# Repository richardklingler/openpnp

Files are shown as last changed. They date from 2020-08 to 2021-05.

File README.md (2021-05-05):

## My OpenPnP pick and place machine stuff

This is a place where a publish all my work building a pick and place machine including mechanics, electronics, Marlin firmware modifications and 3D printed designs.

The machine is driven by the excellent and open sourced [OpenPNP software](http://openpnp.org).

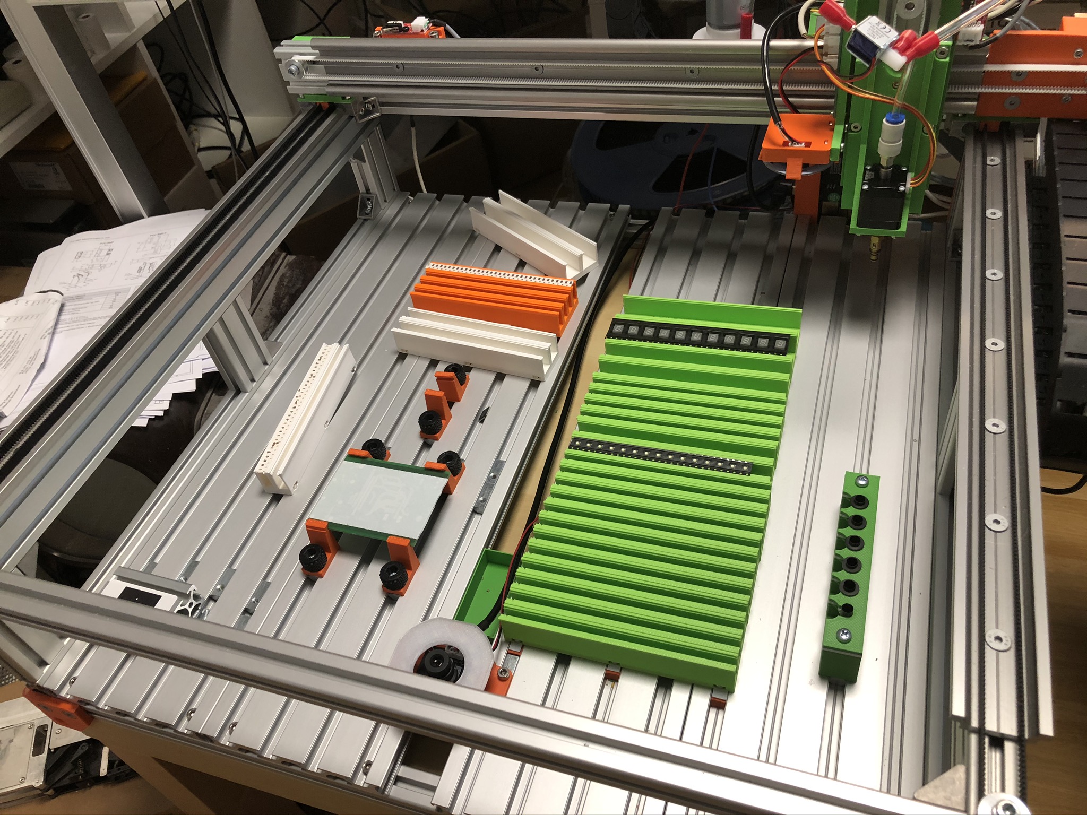
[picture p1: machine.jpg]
My pick and place machine running OpenPNP


### Sponsoring

All required hardware is financed with my low little budget, so every donation is very welcome, either through the Patreon link on the side or through Paypal Me:

[Paypal Me](https://paypal.me/renderingfun)

Currently work is on hold due to missing funds.

### Things to do

This is still a work-in-progress project, so not everything is either published or at final stage. Currently following tasks are ongoing:

#### Z-axis rework

Currently the Z-axis uses Igus slider which are showing high tolerances when pushed/pulled in Y direction. The rails will be therefore replaced with dual MGN9 rails with 2 carriages each for better stability/accuracy. A dual rail design could then also be used for a dual-nozzle setup.

#### X-axis rework

Also the Igus rails on the X-axis are unacceptable. Seems Igus rails are only halfway usable when lying flat, just like for the Y-axis. The new X-axis will use two MGN9 rails, one on top and one at the bottom of the X-axis profile.

### Updates

- 12.09.2020 : Added X belt tensioner mount
- 24.08.2020 : Added vacuum pump mount
- 23.08.2020 : Added OpenSCAD designs for electronics
- 23.08.2020 : Added Y axis OpenSCAD design files
- 15.08.2020 : Updated Tool Changer design
- 14.08.2020 : Added OpenSCAD Camera Mounts
- 14.08.2020 : Added OpenSCAD CP40 Nozzle Holder

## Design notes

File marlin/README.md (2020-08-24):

## Marlin modifications for using with OpenPNP

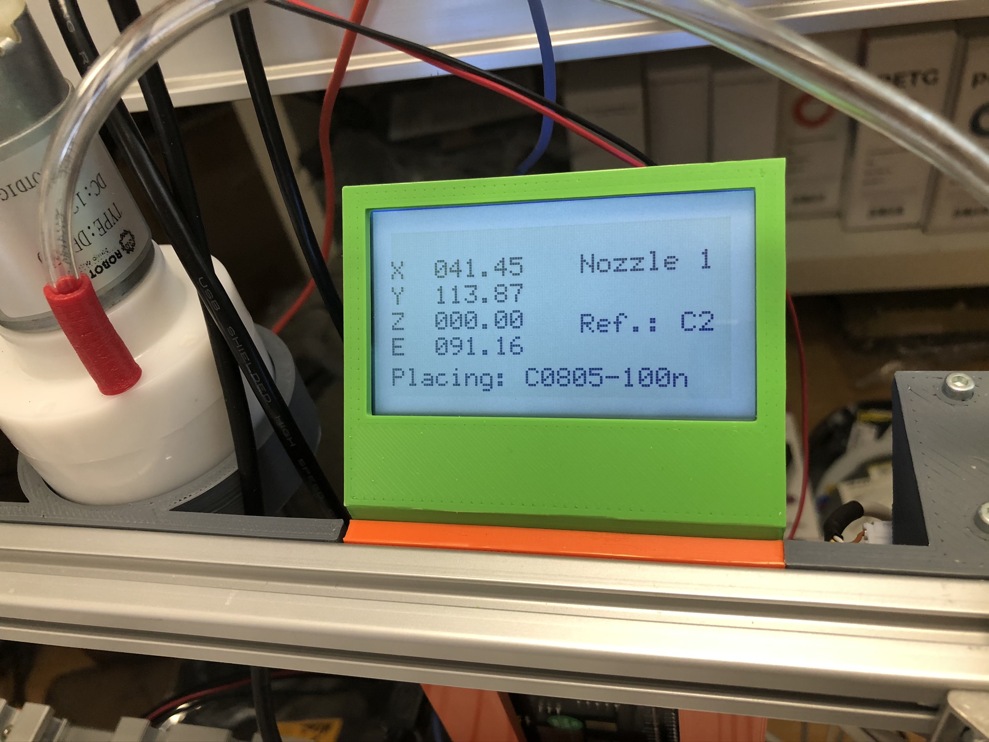
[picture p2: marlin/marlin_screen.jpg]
Marlin Status Screen


Normally Marlin firmware is meant for running a 3d printer, though it has some configuration options to be used for CNC milling and laser cutters.

The most obvious changes are:

- Add dual stepper for Y-axis
- Home position of Z-axis at Z-Max. The Z-axis moves down starting at 0.
- Change XYZ homing bump speed
- Configure outputs to be used for vacuum pump, vacuum valve and LED lighting

The not so easy modifications are for the LCD status screen where we just want to display all coordinates together with what the machine is doing. All 3d printer related icons are removed.

- Remove 3d printer icons
- Layout all coordinates vertically with XXX.XX precision
- Modify the M117 status message Gcode command to add more messages on the screen

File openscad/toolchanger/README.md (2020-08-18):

## Tool Changer for CP40 nozzles

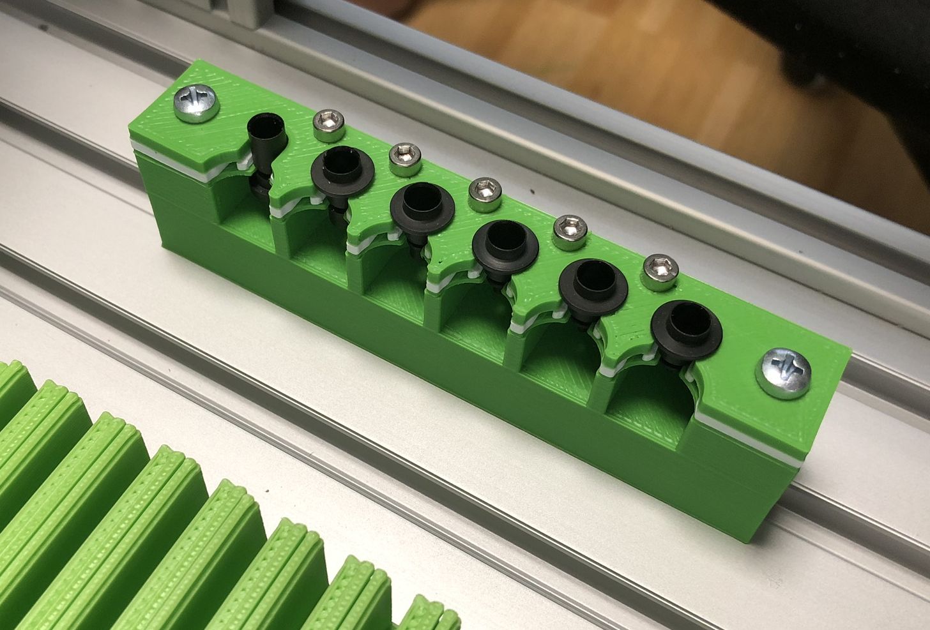
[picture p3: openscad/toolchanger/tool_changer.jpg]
CP40 tool Changer


This is a simple design for CP40 nozzle holder.
The number and the distance betwwen nozzles is configurable in OpenSCAD.

This design uses 4 parts for this:

- Tool_Changer_Mount.scad: Bottom part for mounting all 4 parts to the table. Height has to be adjusted to your needs.
- Tool_Changer_Bottom,scad: A thin layer of 1mm where the nozzles slide in, the thickness is adjusted with the 's' parameter
- Tool_Changer_Middle.scad: This part uses a clamp mechanism so that nozzles stay in place. The force of the clamp can be adjusted with the 'o' parameter'
- Tool_Changer_Top.scad: Top layer which will be screwed down to the table with all other parts

Here is a YouTube video showing how it works:

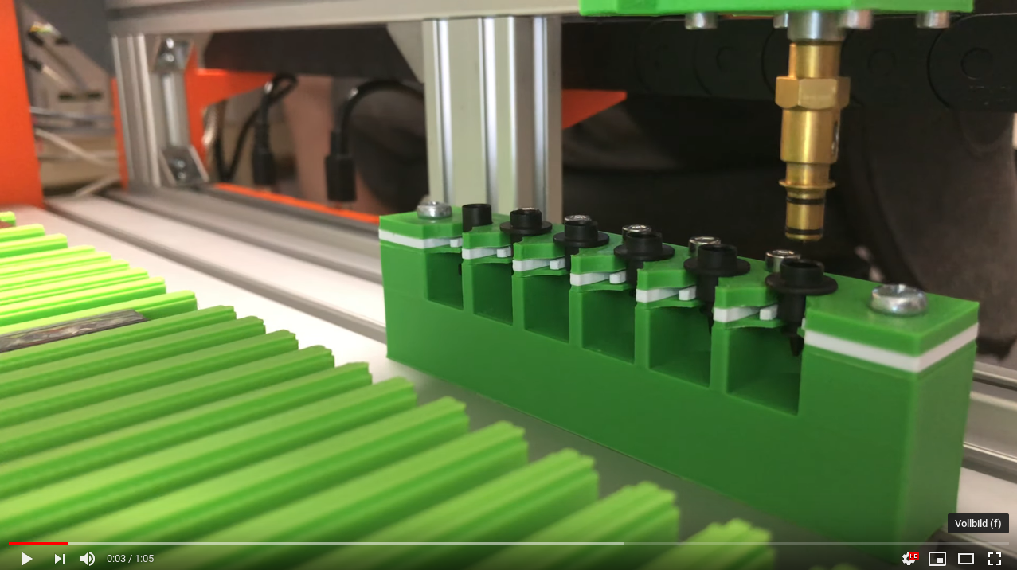
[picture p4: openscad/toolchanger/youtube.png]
CP40 tool changer in action (https://youtu.be/qcL0MLGex4M "CP40 Nozzle Changer")


### 3D Printing

I have printed all parts excep the middler layer which clamps the nozzles with ASA material for its strength.
The clamp itself was printed in PETG as with ASA it starts to bend during printing when you don't use or have a chamber like me (o;

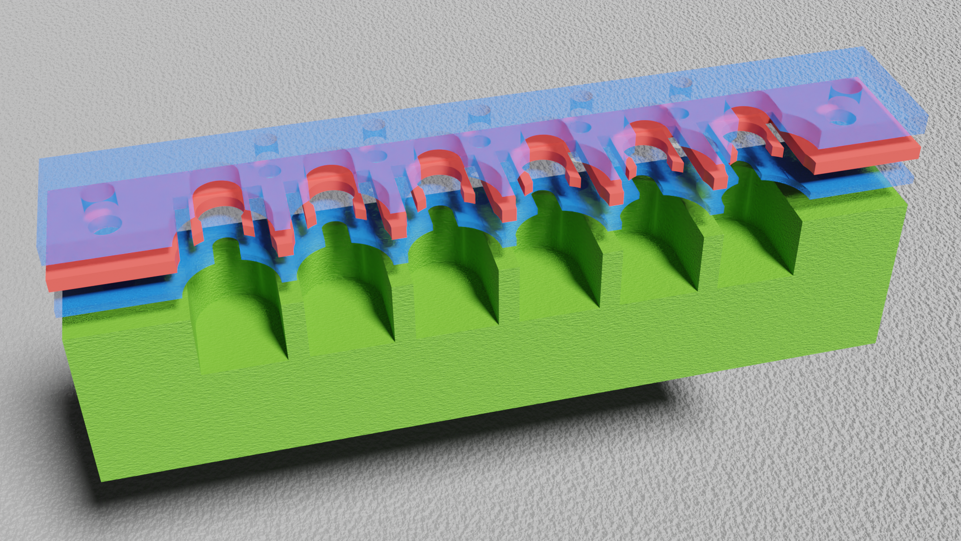
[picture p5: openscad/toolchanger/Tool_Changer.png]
CP40 tool Changer


### Assembly

To mount the tool changer on the machine's table I used M4 x 45 screws....
For clamping all layers together you would (Number of nozzles - 1) M3 x 16 screws and a M3 nut which slides in the bottom mount block at the back.

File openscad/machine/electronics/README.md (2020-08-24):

## Electronics

Here are the OpenSCAD design files for attaching various electronic components to the machine.

### PCB mount for BTT SKR v1.4

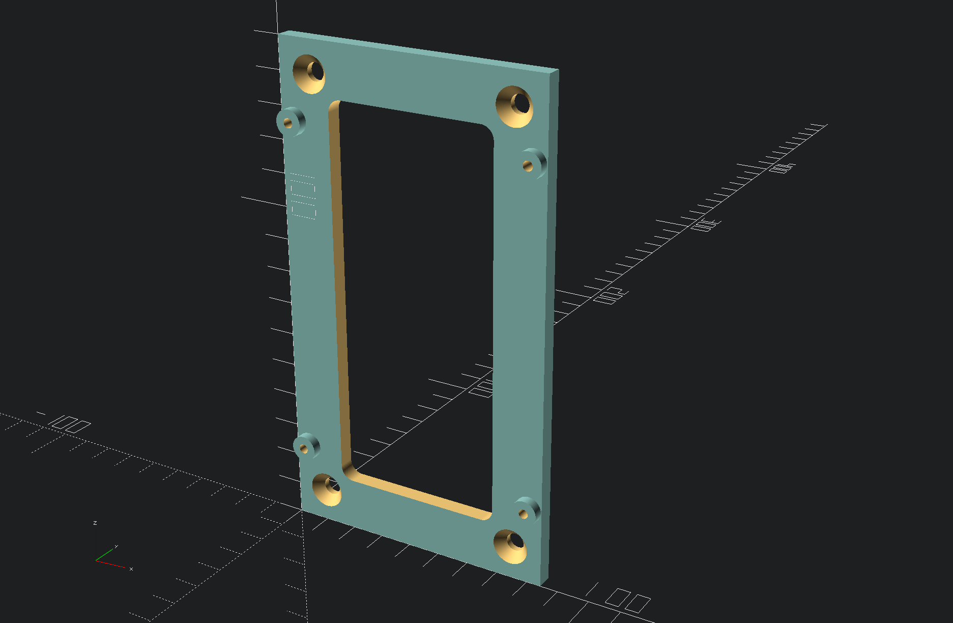
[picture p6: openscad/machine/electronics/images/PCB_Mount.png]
BTT SKR v1.4 mount


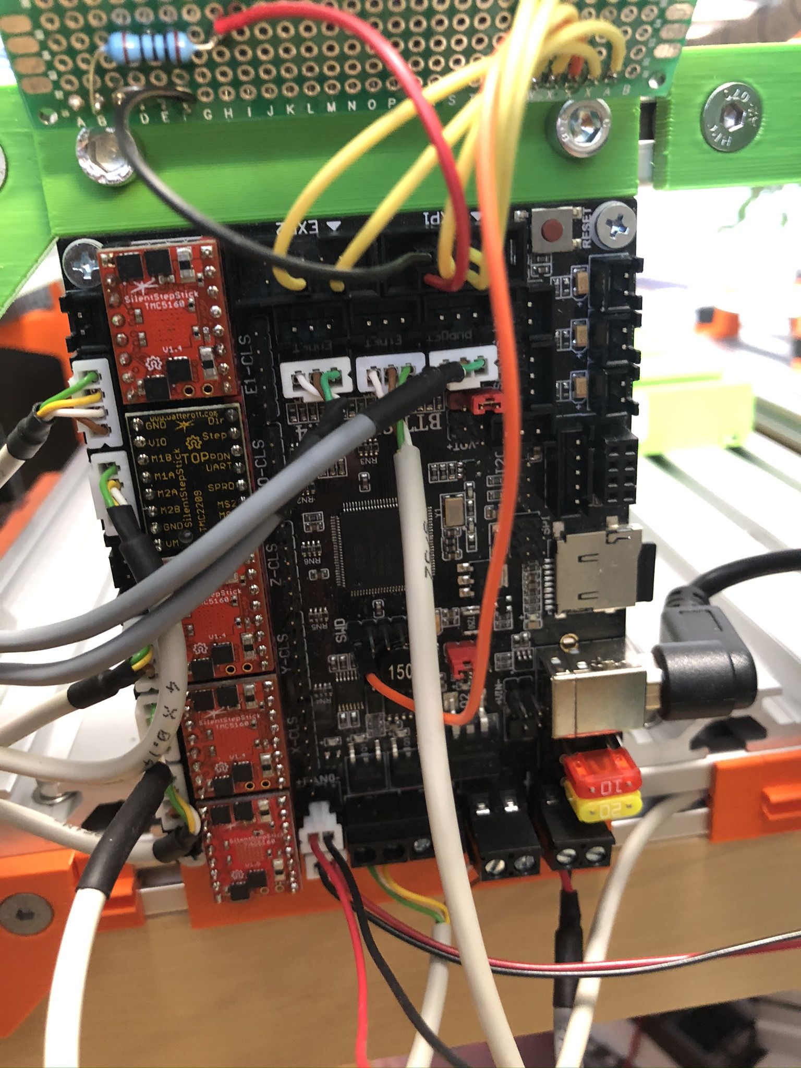
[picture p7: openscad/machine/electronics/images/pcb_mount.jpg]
BTT SKR v1.4 mount


### LCD mount for Newhaven 12864 LC display

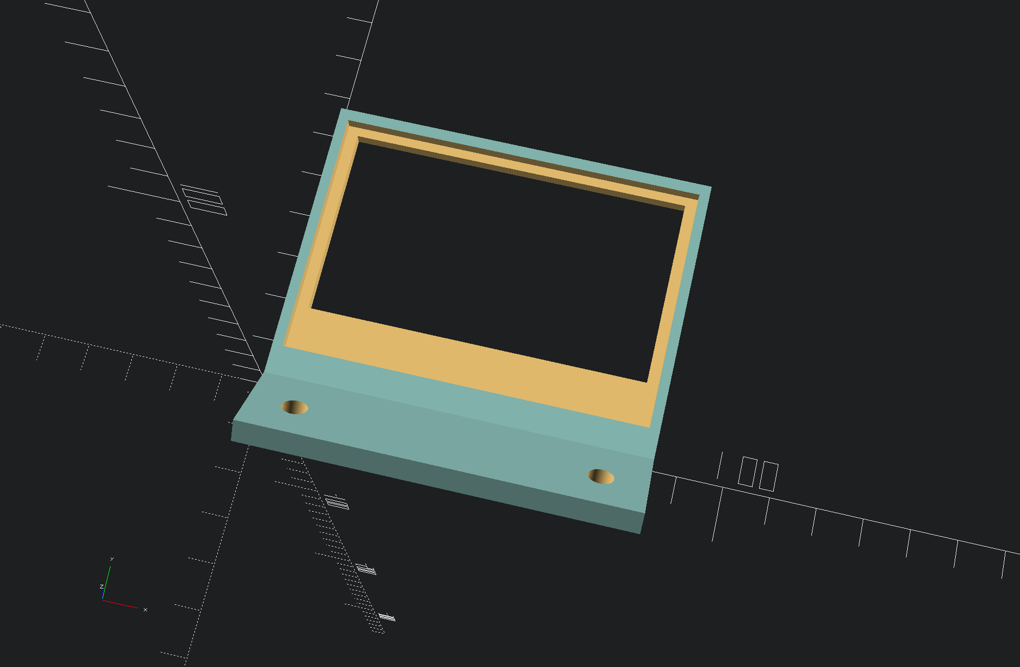
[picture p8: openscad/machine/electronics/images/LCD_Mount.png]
LCD mount


This is a holder for the Newhaven LC display INHD-C12864-1Z-FSW-FB-HTT. It is meant to screw it at the top of the PCB holder as a PCB holder with LCD mount wasn't really printable, so I did a two-part design.

### Power supply mount

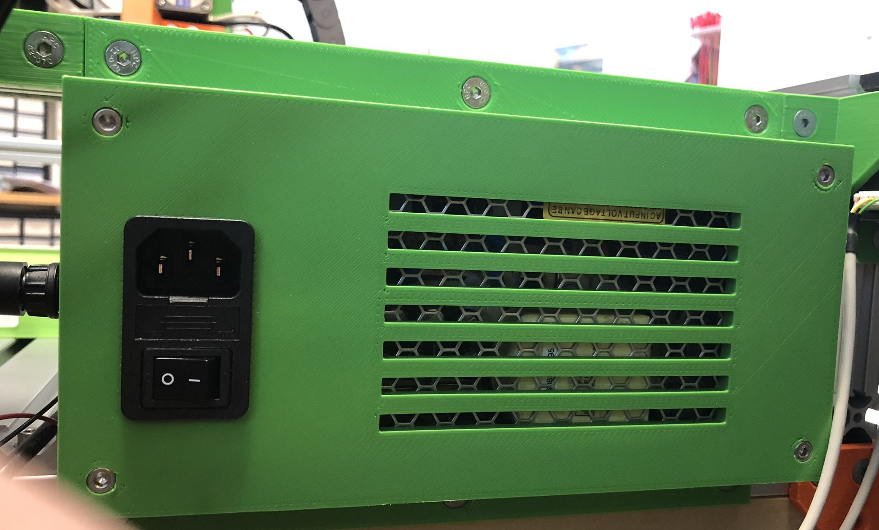
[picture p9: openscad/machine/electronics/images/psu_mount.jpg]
PSU mount


### Vacuum pump holder

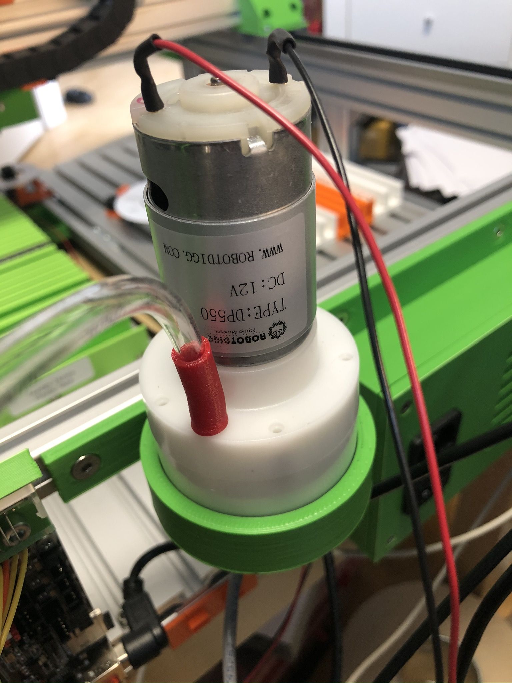
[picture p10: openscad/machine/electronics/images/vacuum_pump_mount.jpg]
Vacuum pump mount


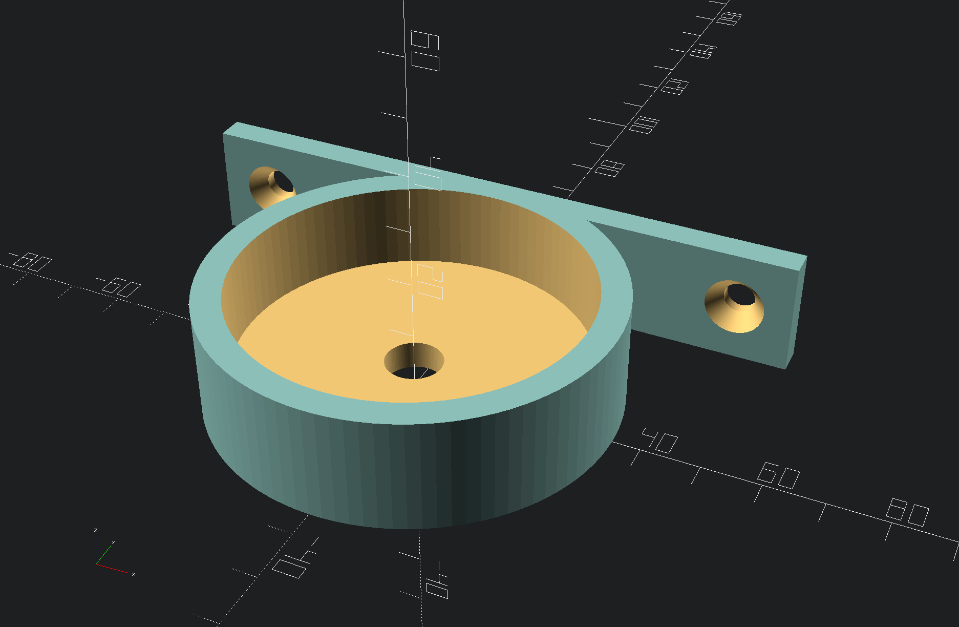
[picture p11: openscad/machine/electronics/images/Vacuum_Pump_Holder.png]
Vacuum pump mount


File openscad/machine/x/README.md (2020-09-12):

## X axis

Here you find my OpenSCAD design files in regards to the X-axis setup.

Be aware that the resulting STL files might give different results in your 3D printer due to different nozzle width and printer settings.

### X belt tensioner

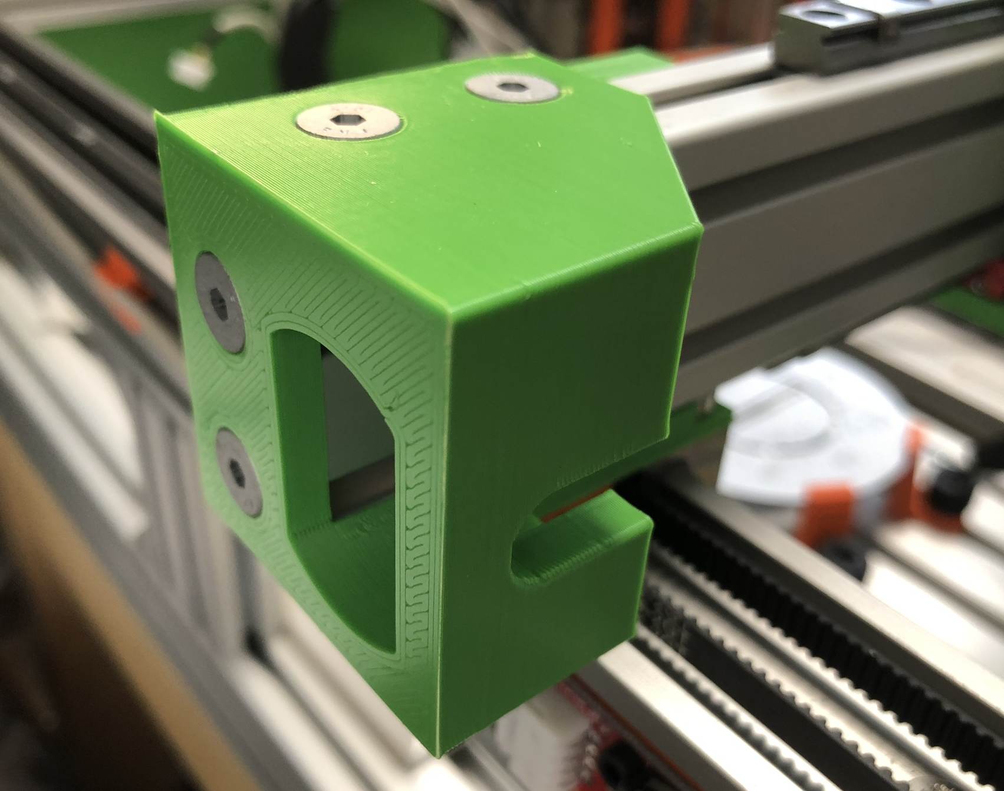
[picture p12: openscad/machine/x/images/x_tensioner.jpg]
X belt tensioner


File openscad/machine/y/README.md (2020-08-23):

## Y axis

Here you find my OpenSCAD design files in regards to the dual Y-axis setup.

Be aware that the resulting STL files might give different results in your 3D printer due to different nozzle width and printer settings.

### Y motor mount

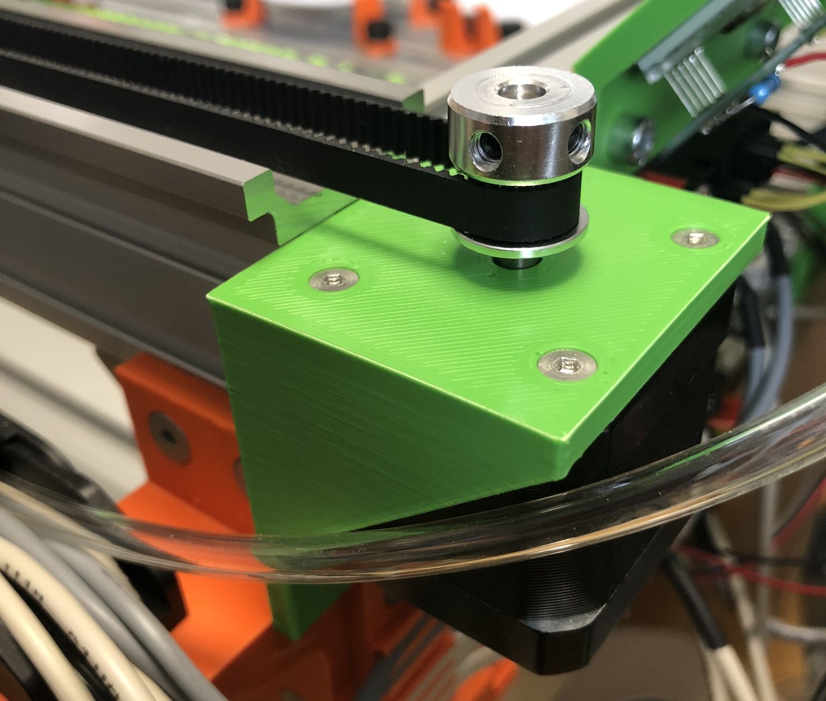
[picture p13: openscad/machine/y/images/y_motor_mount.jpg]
Y Motor Mount


The Y motor mount takes a Nema 17 motor with a width of 42mm mounted with 4 M3x8 counter sunk head screws. It is mounted with 3 M5x10 counter sunk head screws directly at the back of machine on the aluminum frame. There is only one design file, so for printing both sides you have to mirror one mesh in your slicer software.

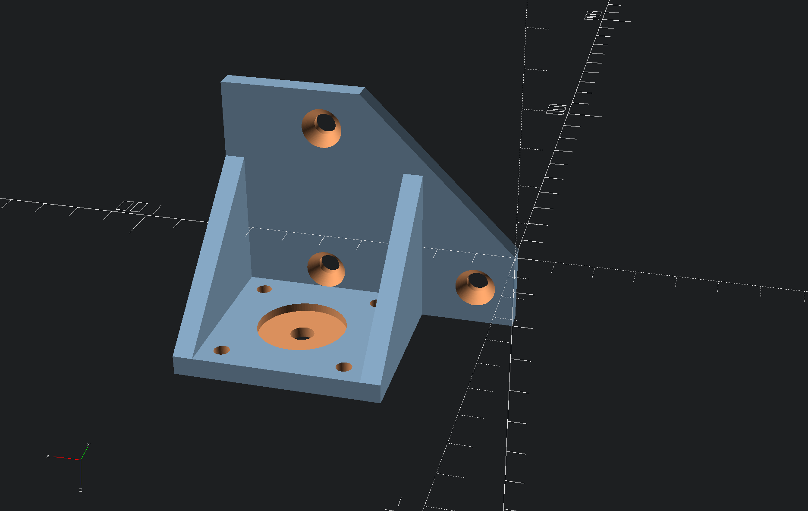
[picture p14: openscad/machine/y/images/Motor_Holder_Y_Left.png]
Y Motor Mount


### Y belt tensioner

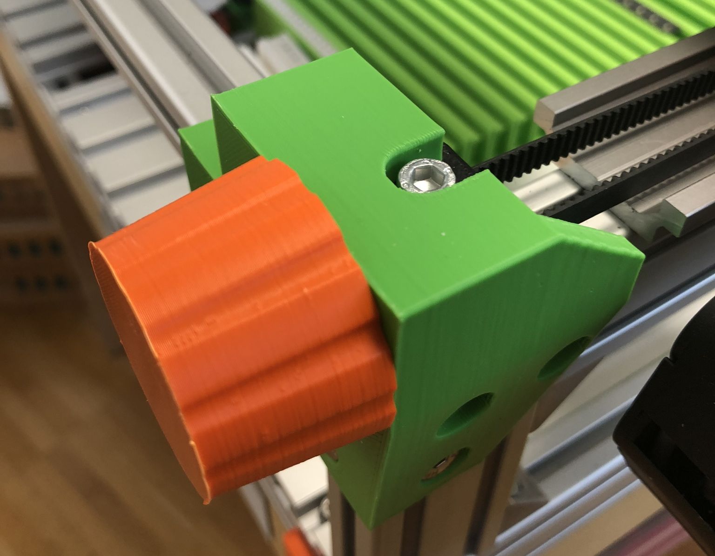
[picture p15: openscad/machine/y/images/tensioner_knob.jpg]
Y Belt Tensioner


The belt tensioner for the y-axis consists of three parts:

    - Tensioner screw
    - Tensioner knob
    - Tensioner mount

For the thread I used this thingiverse OpenSCAD library:

[OpenScad library. Threads for screws and nuts V1](https://www.thingiverse.com/thing:3131126)

For better durability I printed those parts (as most parts of my machine) with ASA filament. It is advisable to print the screw and the knob with a layer height not greater than 0.2mm. Also for both sides for the tensioner mount you have to mirror one mesh in your slicer.

### X rail mounts

The X rail mounts are designed to be screwed directly onto Igus slider blocks. Also they hold at the bottom the GT2 belt clamp mechanism. Igus rails were chosen for the Y-axis as a 6mm wide GT2 belt fits perfectly between rails and slider block.

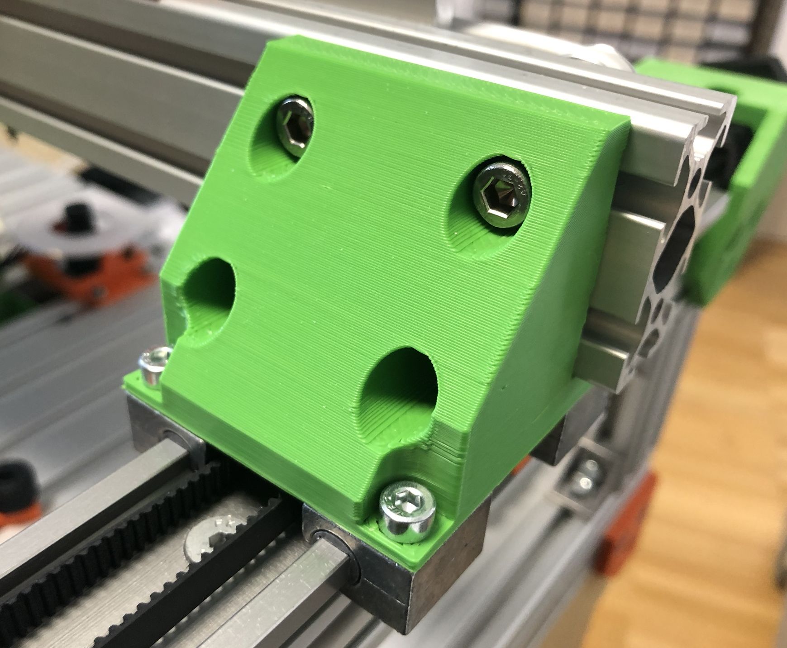
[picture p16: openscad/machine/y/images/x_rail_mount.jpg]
X Rail Mount


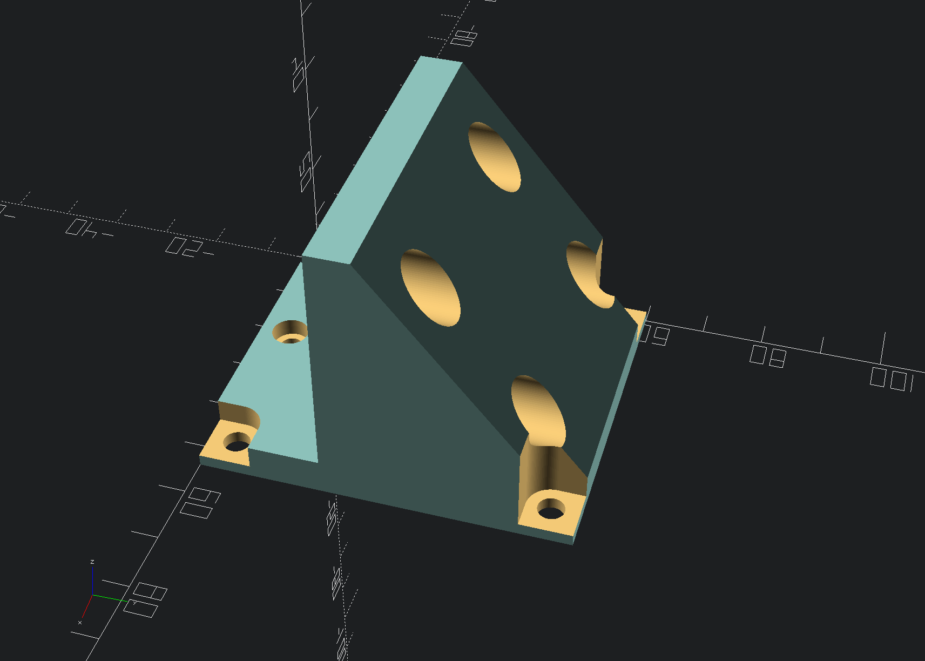
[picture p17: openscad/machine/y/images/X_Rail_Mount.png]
X Rail Mount


### GT2 clamp

This is a preliminary design as I think that it might be the cause for some backslash in the Y-axis.

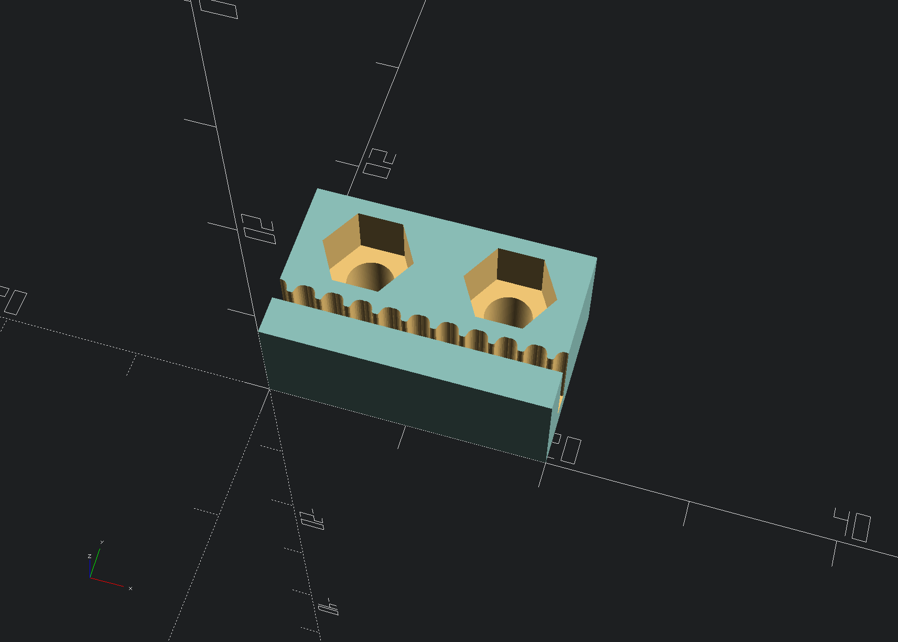
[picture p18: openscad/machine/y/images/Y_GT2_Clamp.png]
Y belt GT2 clamp


The GT2 clamp which mounts directly under the X-rail mounts uses a GT2 timing belt OpenSCAD module used for cutting out the profile. Depending on the thickness of the belt you might want to adjust this section:

    translate([-2, 3.35, 6]) belt_len(profile = tGT2_2, belt_width = 8, len = 100);
    translate([-2.2, 3.5, 6]) belt_len(profile = tGT2_2, belt_width = 8, len = 100);
    translate([-1.9, 3.5, 6]) belt_len(profile = tGT2_2, belt_width = 8, len = 100);

It just cuts out the GT2 slot at slightly different location to accommodate for thicker belts. You might want to do some test prints and check with your GT2 belt if it fits perfectly and doesn't causes any backslash.

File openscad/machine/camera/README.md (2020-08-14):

## Camera mounts

This directory contains OpenSCAD design files for my camera mounts and a LED diffuser.

### Bottom mount

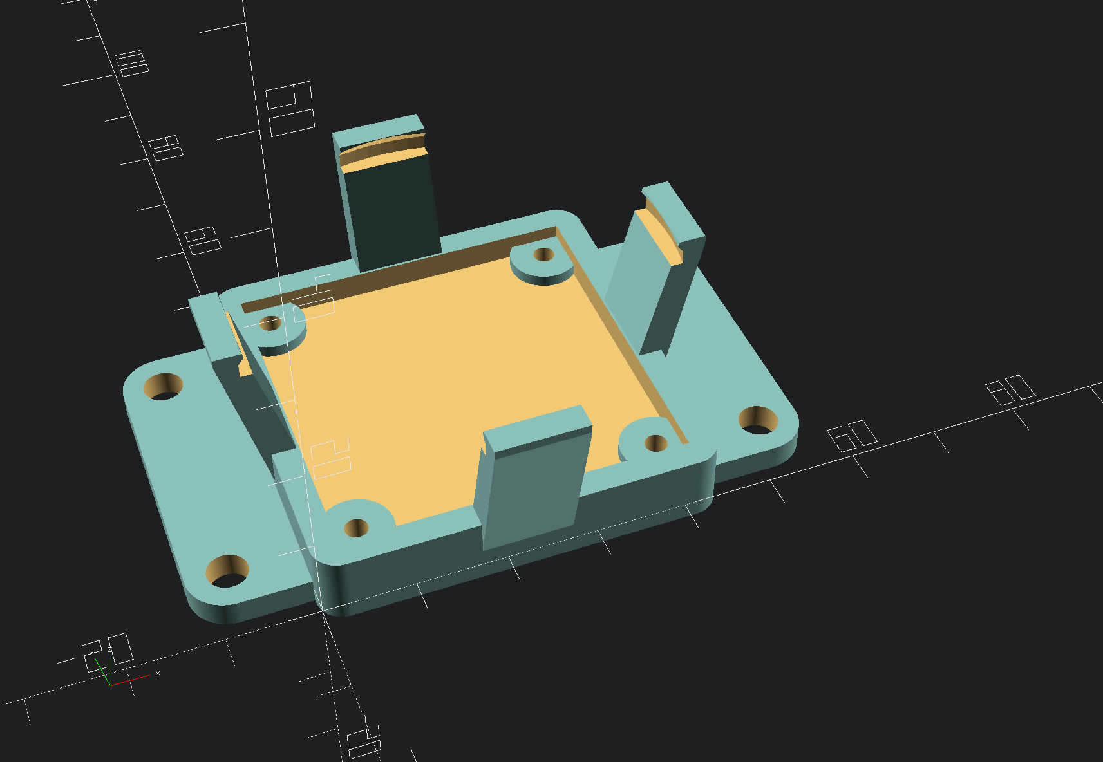
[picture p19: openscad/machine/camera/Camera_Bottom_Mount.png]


This is for a square PCB USB camera you can find on Ebay.

### Top mount

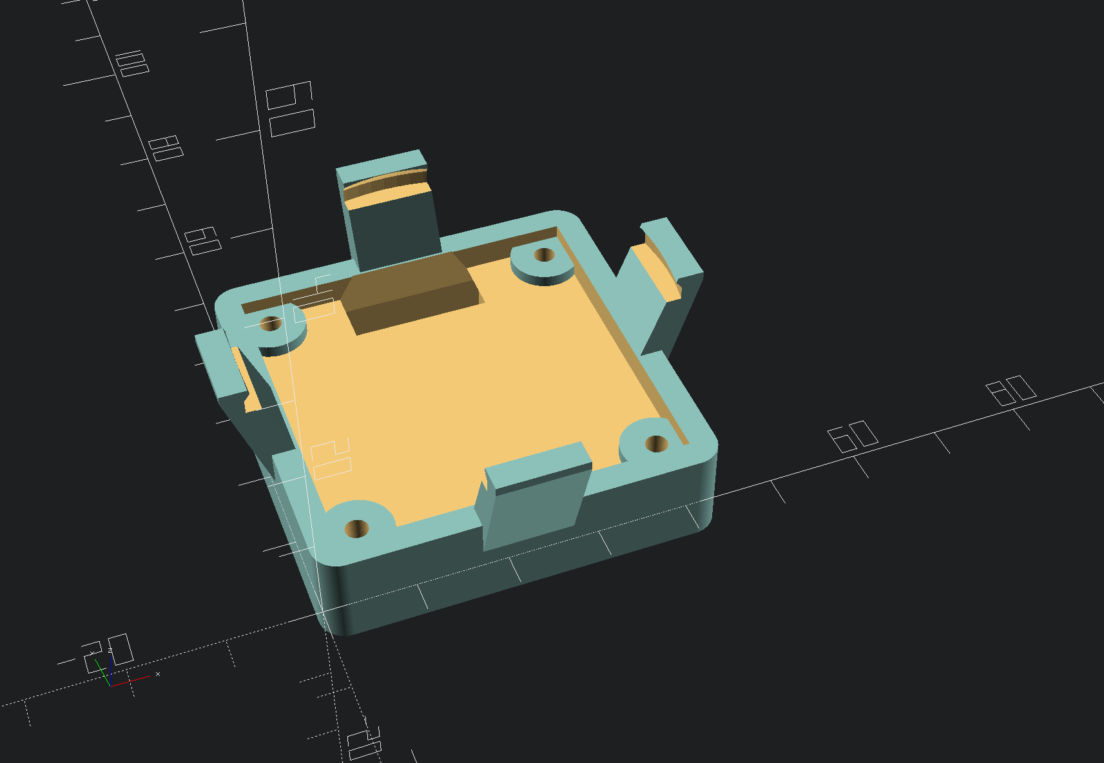
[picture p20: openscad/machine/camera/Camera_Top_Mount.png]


This is for the same sized USB camera as the one mounted at the bottom but contains a square hole if yo uwant to resolder the JST PH 2.0 connecter on the back of the PCB.

### Lens adapter

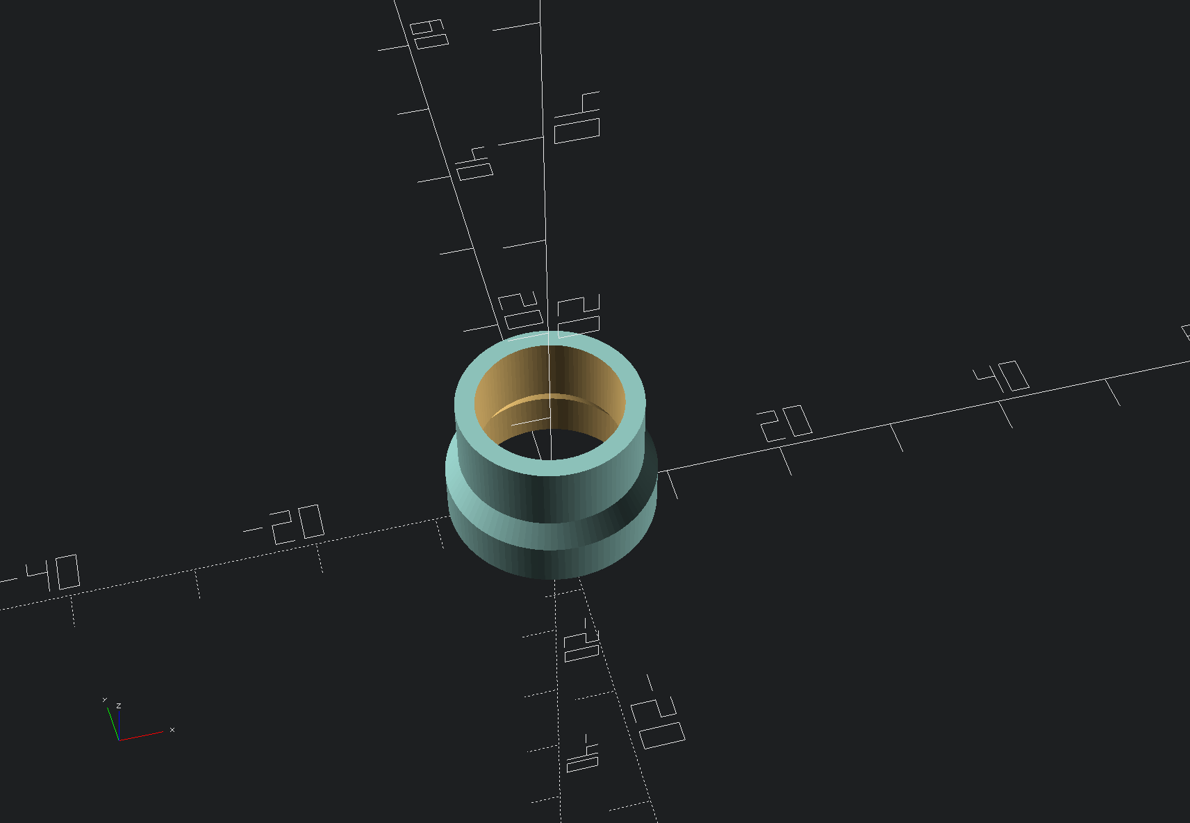
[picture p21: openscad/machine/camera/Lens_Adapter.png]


During experimenting with different lenses it turned out that
the M12 0.5mm thread on those camera are too short to focus close objects.

This adapter just snaps onto the camera's thread end extends the focal distance.

### LED diffuser

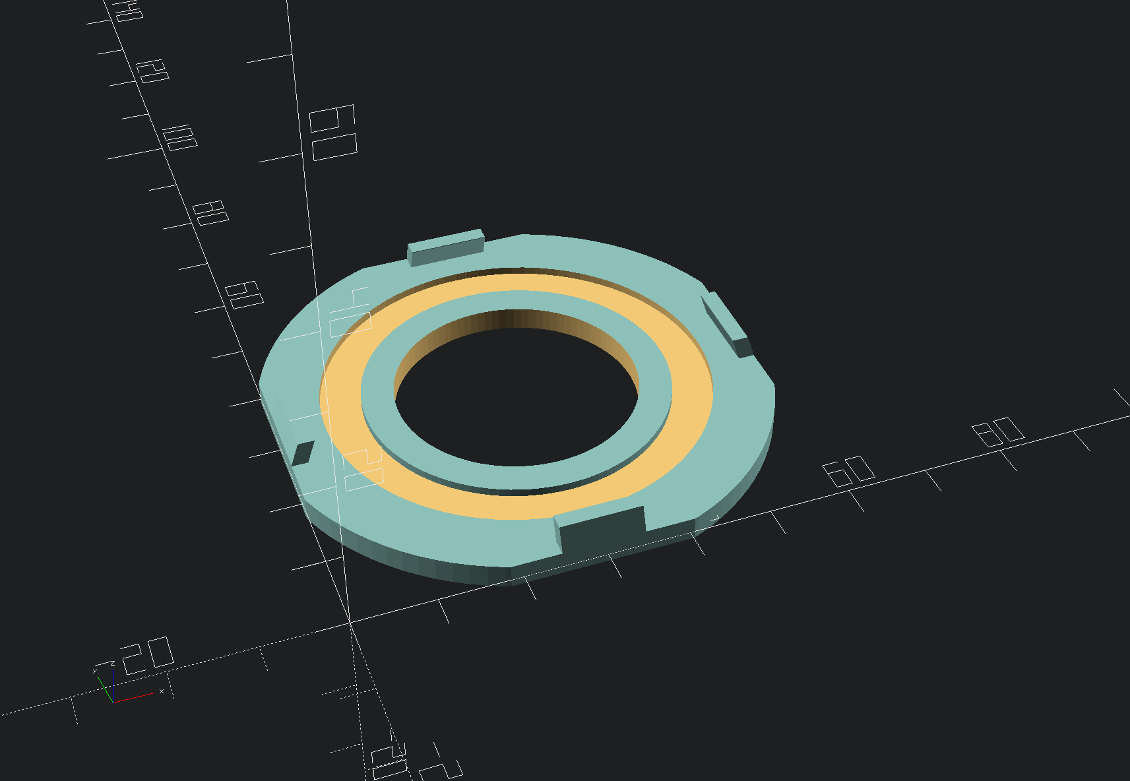
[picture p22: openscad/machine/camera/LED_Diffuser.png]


This diffuser should be printed with transparent PLA or PETG.
You might want to play with the infill percentage and infill angle.

You can just snap on the camera mounts above.

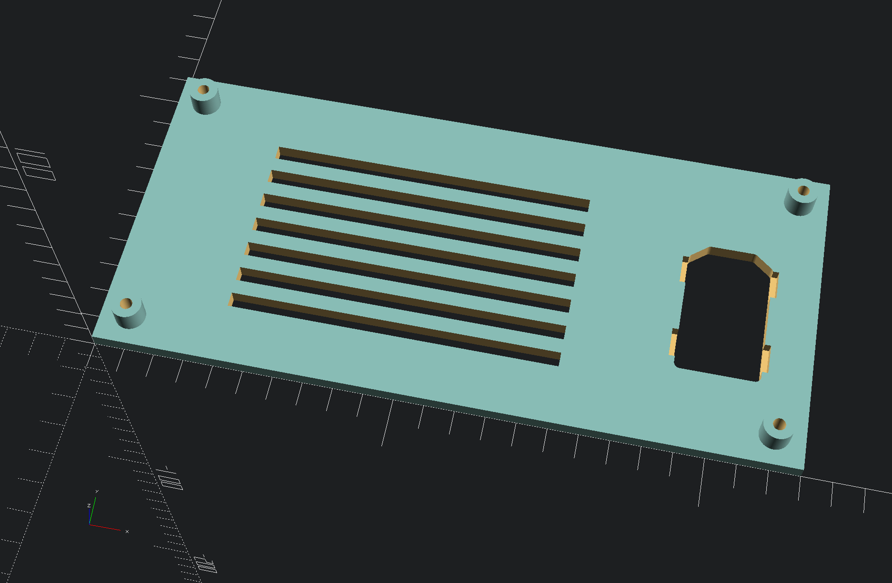
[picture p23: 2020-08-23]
openscad/machine/electronics/images/Power_Supply_Cover.png

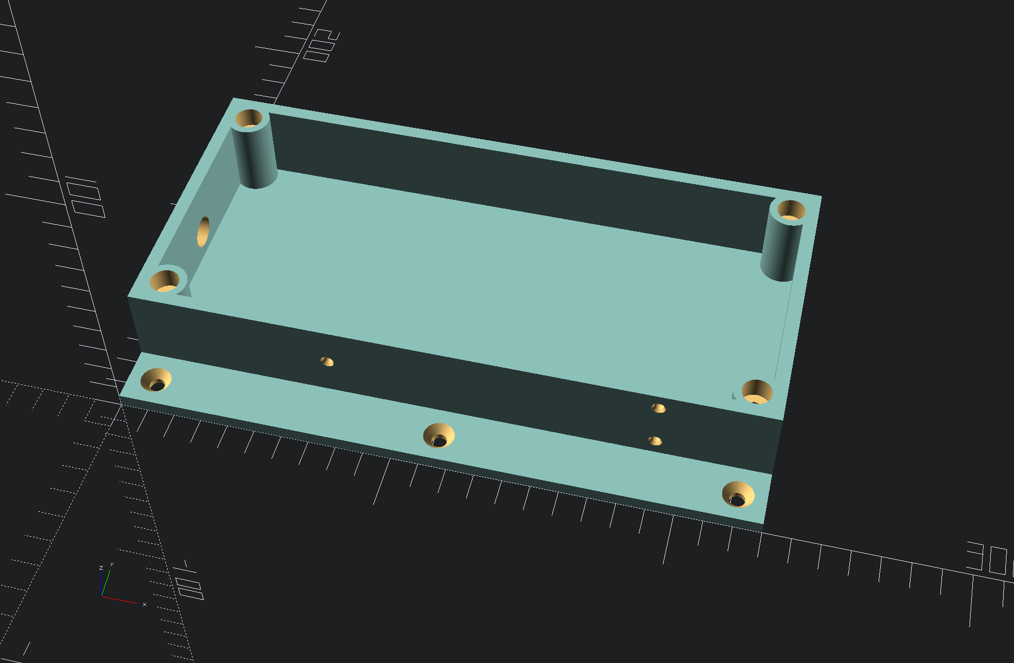
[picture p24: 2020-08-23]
openscad/machine/electronics/images/Power_Supply_Case.png

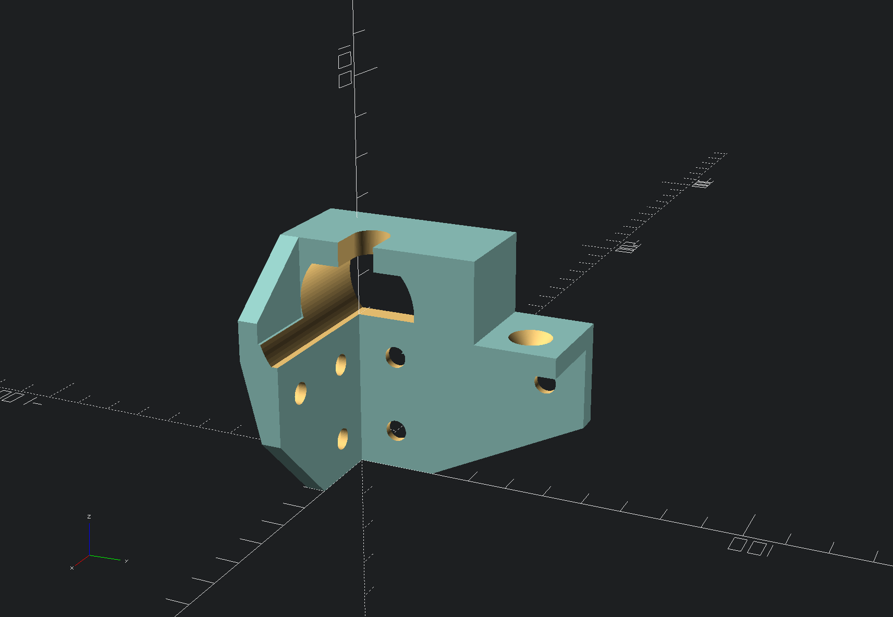
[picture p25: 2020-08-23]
openscad/machine/y/images/Y_Tensioner_Right.png

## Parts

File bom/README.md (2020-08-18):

## Bill of materials

Here a list of parts I used in my machine

### Frame construction

The base frame consists mainly out of 20x20 and 40x20 profile elements.
You are free to use different lengths if you want your machine to be bigger or smaller.
I just made them that way so the base frame fits onto an Ikea Lack table which measures 550mm x 550mm.

#### Frame parts list

    4 * 550mm 40x20 profile 5
    6 *  70mm 40x20 profile 5
    4 * 510mm 20x20 profile 5

#### Table top

For the table top I used 120x15 profile 8. Many people use a steel sheet as a surface to use magnet holders for their PCBs and strip feeders.
But I decided to go with the profile 8 version so I can slide in those T-nuts for screwing down the PCB holders and the bottom camera.

With the 4 * 120mm width I get a gap of 30mm, which I decided to place it in the middle so the table is divided in two parts: PCs left, strip feeders right and the bottom camera and discard box in the middle.

    4 * 550m 15x120 profile 8

### Electronics

#### Controller board

For the time being I use a BTT SKR v1.4 board running the Marlin firmware with little modification for the LCD screen.
The stepper drivers are Trinamic silent step stick.

At a later stage I will design my own ctronller board more suitable for OpenPNP with separate power rails for steppers, lighting, valves and pumps based on a STM32F4 MCU.

    1 * BTT SKR v1.4 controller board
    4 * TMC5160 silent step stick for X, 2 * Y and Z
    1 * TMC2209 silent step stick for the pick head motor

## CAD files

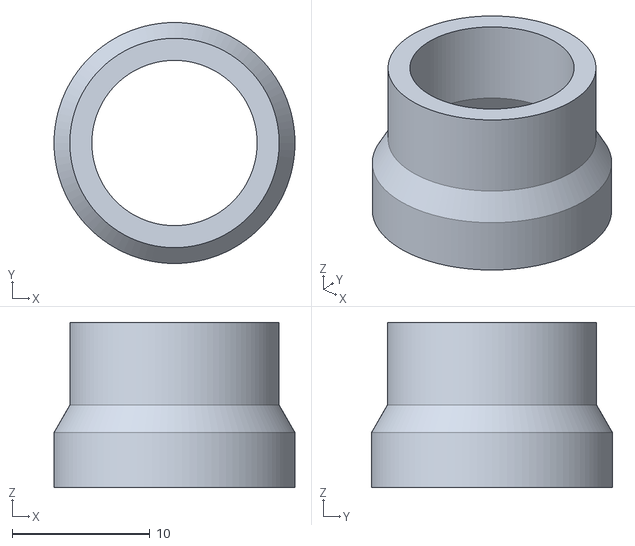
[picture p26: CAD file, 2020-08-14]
openscad/machine/camera/stl/Lens_Adapter.stl
17.5 x 17.5 x 12.0

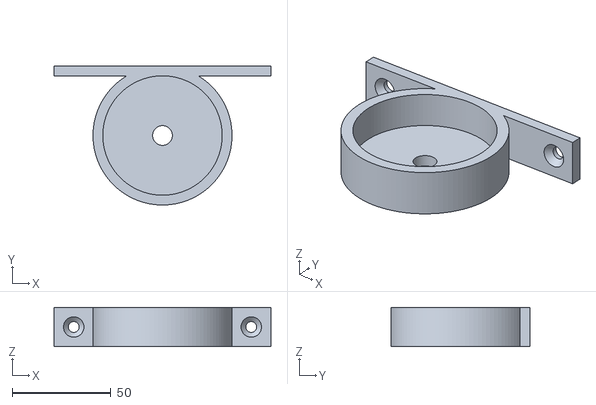
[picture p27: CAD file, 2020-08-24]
openscad/machine/electronics/stl/Vacuum_Pump_Holder.stl
110.0 x 70.5 x 20.0

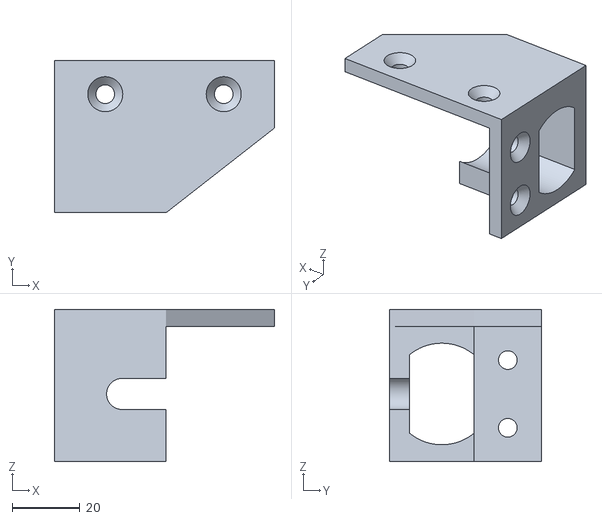
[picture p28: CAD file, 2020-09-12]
openscad/machine/x/stl/X_Tensioner_Mount.stl
65.0 x 45.0 x 45.0

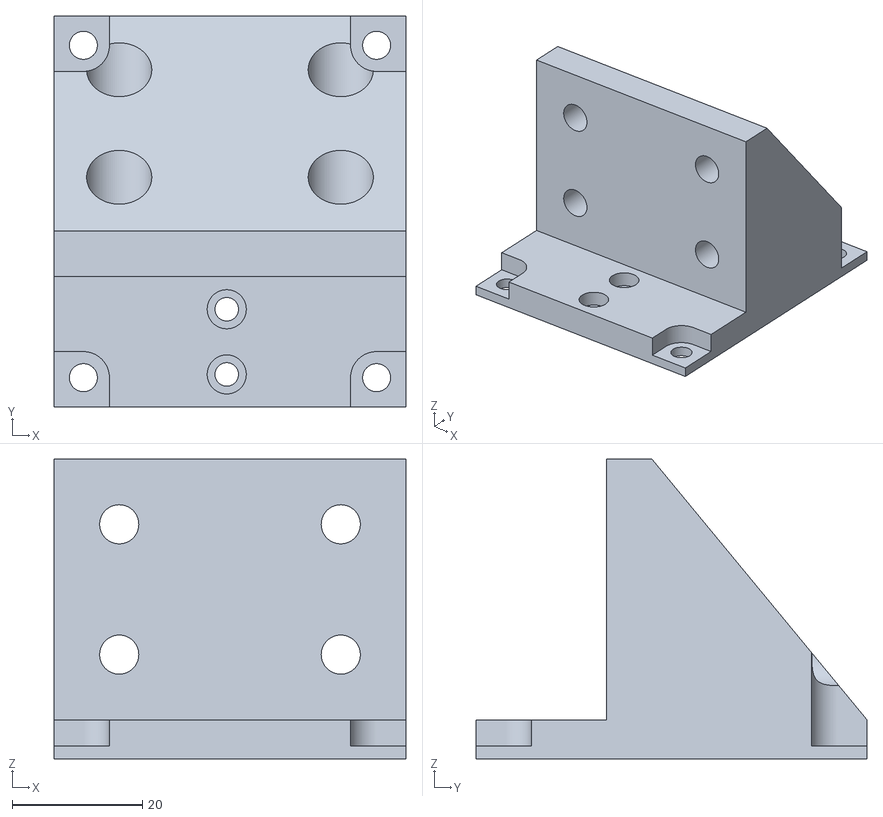
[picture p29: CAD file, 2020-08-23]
openscad/machine/y/stl/X_Rail_Mount.stl
54.0 x 60.0 x 46.0

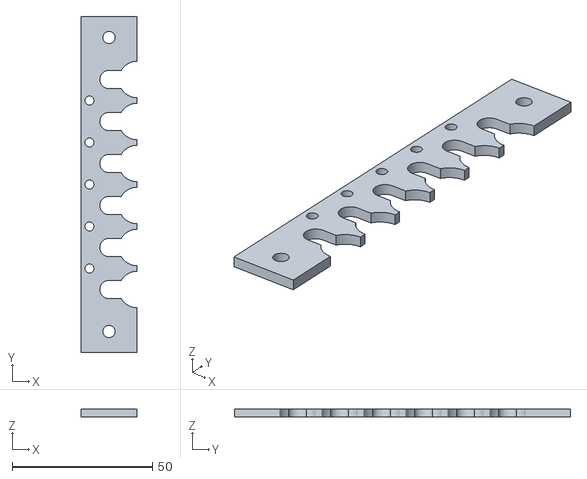
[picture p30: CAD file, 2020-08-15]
openscad/toolchanger/stl/Tool_Changer_Top.stl
20.0 x 120.0 x 3.00

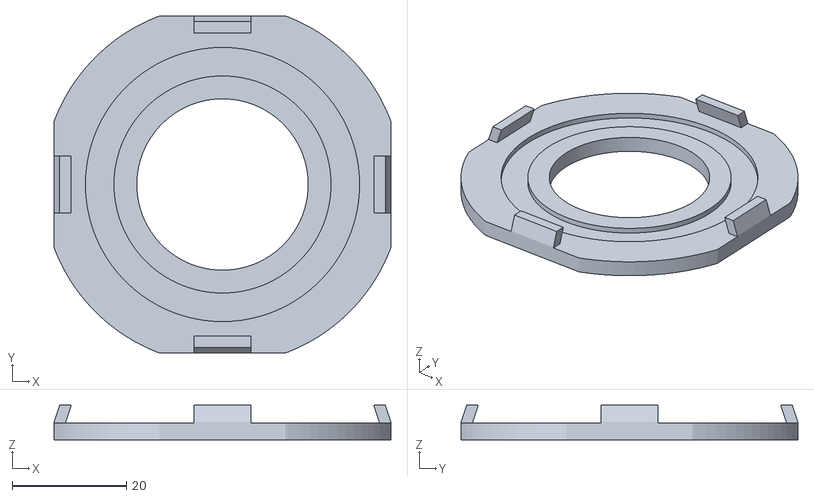
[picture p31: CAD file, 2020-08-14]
openscad/machine/camera/stl/LED_Diffuser.stl
59.0 x 59.0 x 6.10

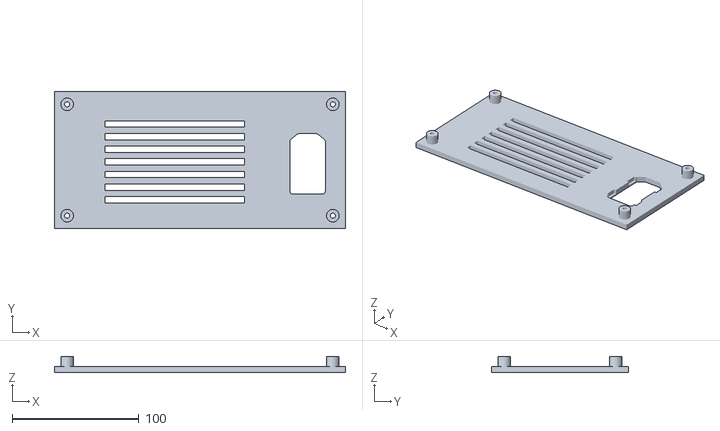
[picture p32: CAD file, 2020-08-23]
openscad/machine/electronics/stl/Power_Supply_Cover.stl
230.0 x 108.0 x 13.0

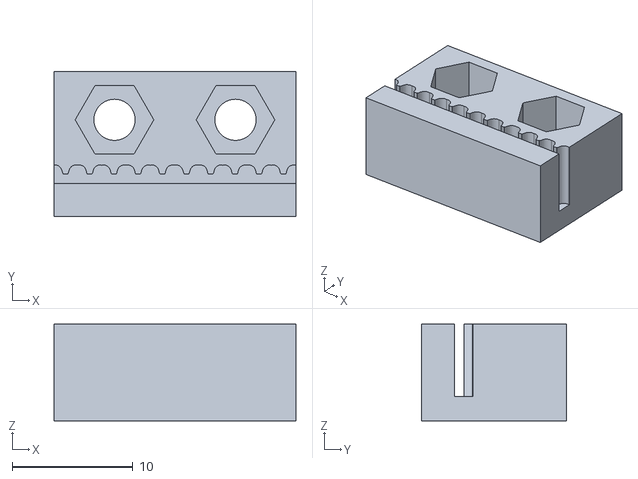
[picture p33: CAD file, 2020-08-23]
openscad/machine/y/stl/Y_GT2_Clamp.stl
20.0 x 12.0 x 8.00

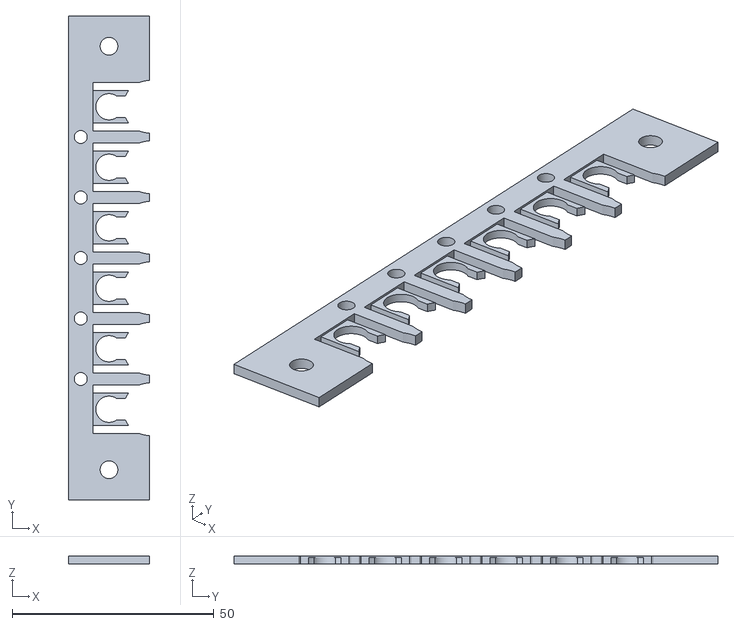
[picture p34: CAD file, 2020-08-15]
openscad/toolchanger/stl/Tool_Changer_Middle.stl
20.0 x 120.0 x 2.00

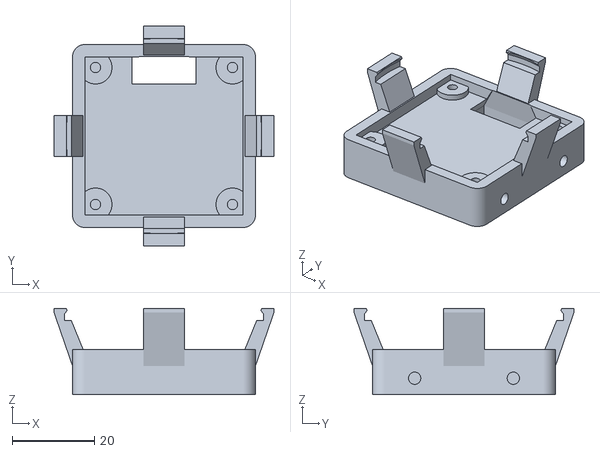
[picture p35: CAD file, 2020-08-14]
openscad/machine/camera/stl/Camera_Top_Mount.stl
53.5 x 53.5 x 21.0

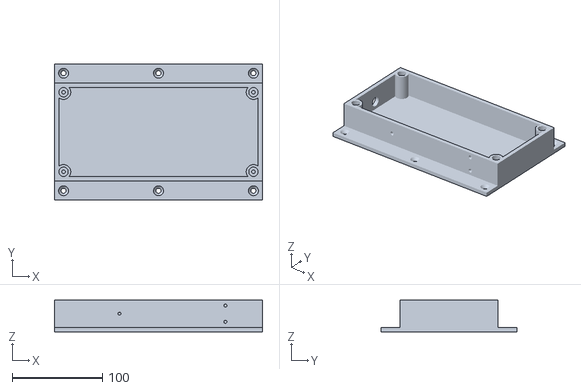
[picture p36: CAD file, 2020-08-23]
openscad/machine/electronics/stl/Power_Supply_Case.stl
230.0 x 150.0 x 35.0

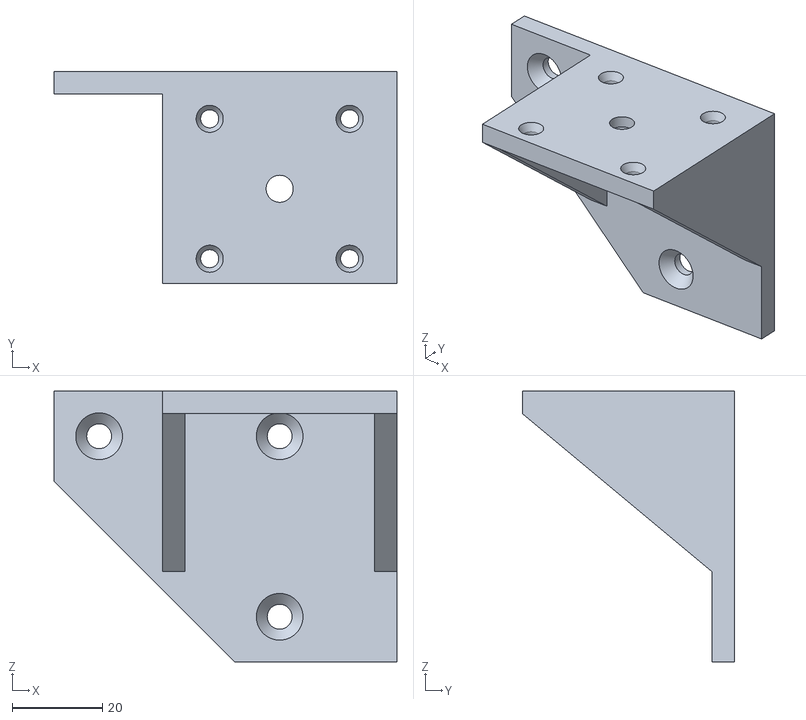
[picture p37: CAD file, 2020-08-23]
openscad/machine/y/stl/Motor_Holder_Y_Left.stl
76.0 x 47.0 x 60.0

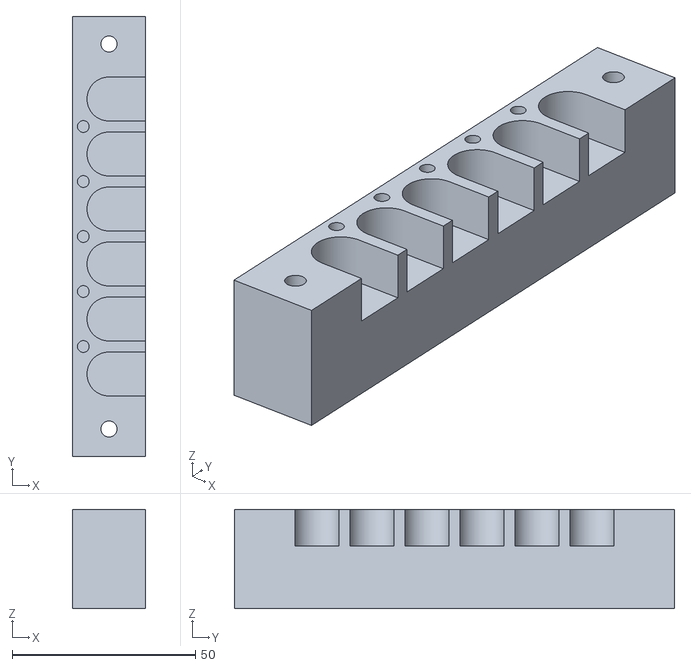
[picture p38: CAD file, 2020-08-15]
openscad/toolchanger/stl/Tool_Changer_Mount.stl
20.0 x 120.0 x 27.0

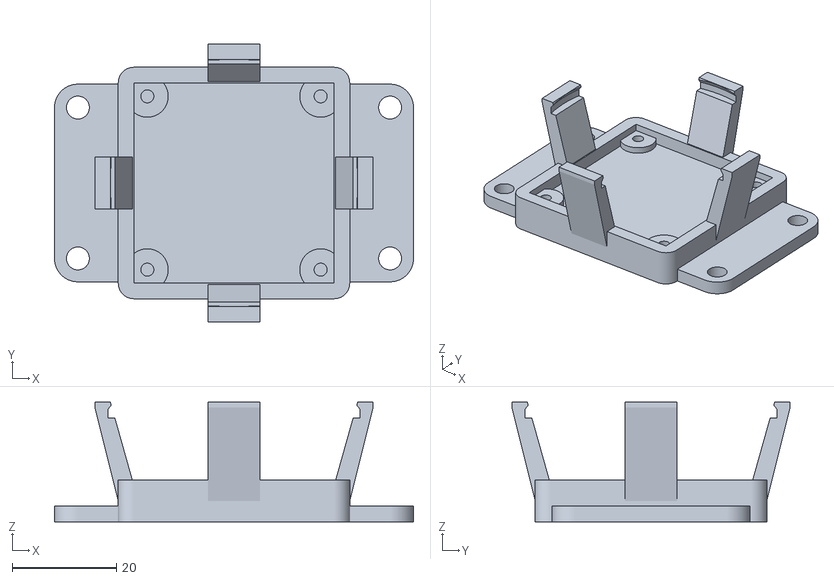
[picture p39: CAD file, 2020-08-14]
openscad/machine/camera/stl/Camera_Bottom_Mount.stl
69.0 x 53.5 x 23.0

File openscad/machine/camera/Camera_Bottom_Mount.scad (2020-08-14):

$fn = 100;

t = 3;
pcb = 1.6;

// Inner/outer radius of LED ring
r1 = 49.5 / 2;
r2 = 34.3 / 2;

// Camera module width
cw = 38.5;
// Camera module screw distance
cs = 33.3;
sr = 2.5 / 2;
// Camera connector
cl = 11;
ch = 6;

w = cw + 2 * t;
l = 60;

difference()
{
    union()
    {
        hull()
        {
            translate([- (l - w) / 2, (l - w) / 2, -2]) cylinder(3, 4.5, 4.5);
            translate([(l + w) / 2, (l - w) / 2, -2]) cylinder(3, 4.5, 4.5);
            translate([(l + w) / 2, w - (l - w) / 2, -2]) cylinder(3, 4.5, 4.5);
            translate([- (l - w) / 2, w - (l - w) / 2, -2]) cylinder(3, 4.5, 4.5);
        }
        hull()
        {
            translate([t, t, -2]) cylinder(8, t, t);
            translate([cw + t, t, -2]) cylinder(8, t, t);
            translate([cw + t, cw + t, -2]) cylinder(8, t, t);
            translate([t, cw + t, -2]) cylinder(8, t, t);
        }
        // LED ring holder
        hull()
        {
            translate([0, t + cw / 2 - 5, 2]) cube([t, 10, t], 0); 
            translate([t + cw / 2 - r1 - t + 1, t + cw / 2 - 5, 20]) cube([t, 10, 1], 0); 
        }
        hull()
        {
            translate([cw + t, t + cw / 2 - 5, 2]) cube([t, 10, t], 0); 
            translate([t + cw / 2 + r1 - 1, t + cw / 2 - 5, 20]) cube([t, 10, 1], 0); 
        }
        rotate([0, 0, 90])
        translate([0, -cw  - 2 * t, 0])
        hull()
        {
            translate([0, t + cw / 2 - 5, 2]) cube([t, 10, t], 0); 
            translate([t + cw / 2 - r1 - t + 1, t + cw / 2 - 5, 20]) cube([t, 10, 1], 0); 
        }
        rotate([0, 0, 90])
        translate([0, -cw  - 2 * t, 0])
        hull()
        {
            translate([cw + t, t + cw / 2 - 5, 2]) cube([t, 10, t], 0); 
            translate([t + cw / 2 + r1 - 1, t + cw / 2 - 5, 20]) cube([t, 10, 1], 0); 
        }
    }
    // Bottom rail mounts
    translate([- (l - w) / 2, (l - w) / 2, -6]) cylinder(12, 2.2, 2.2);
    translate([- (l - w) / 2 + 60, (l - w) / 2, -6]) cylinder(12, 2.2, 2.2);
    translate([(l + w) / 2, w - (l - w) / 2, -6]) cylinder(12, 2.2, 2.2);
    translate([- (l - w) / 2, w - (l - w) / 2, -6]) cylinder(12, 2.2, 2.2);

    // Camera board cut-out
    translate([t, t, t]) cube([cw, cw, 2 * t], false);

    // Camera screws
    translate([t + (cw - cs) / 2, t + (cw - cs) / 2, -1]) cylinder(2 * t + 2, sr, sr);
    translate([t + cw / 2 + cs / 2, t + (cw - cs) / 2, -1]) cylinder(2 * t + 2, sr, sr);
    translate([t + cw / 2 + cs / 2, t + cw / 2 + cs / 2, -1]) cylinder(2 * t + 2, sr, sr);
    translate([t + (cw - cs) / 2, t + cw / 2 + cs / 2, -1]) cylinder(2 * t + 2, sr, sr);
    
    // LED ring
    hull()
    {
        translate([t + cw / 2, t + cw / 2, 13 + 5]) cylinder(pcb, r1, r1);
        translate([t + cw / 2, t + cw / 2, 30 + 5]) cylinder(1, r1 / 2, r1 / 2);
    }
}
difference()
{
    union()
    {
        // Camera screws
        translate([t + (cw - cs) / 2, t + (cw - cs) / 2, t]) cylinder(t - pcb, 4, 4);
        translate([t + cw / 2 + cs / 2, t + (cw - cs) / 2, t]) cylinder(t - pcb, 4, 4);
        translate([t + cw / 2 + cs / 2, t + cw / 2 + cs / 2, t]) cylinder(t - pcb, 4, 4);
        translate([t + (cw - cs) / 2, t + cw / 2 + cs / 2, t]) cylinder(t - pcb, 4, 4);
    }
    // Camera screws
    translate([t + (cw - cs) / 2, t + (cw - cs) / 2, -1]) cylinder(2 * t + 2, sr, sr);
    translate([t + cw / 2 + cs / 2, t + (cw - cs) / 2, -1]) cylinder(2 * t + 2, sr, sr);
    translate([t + cw / 2 + cs / 2, t + cw / 2 + cs / 2, -1]) cylinder(2 * t + 2, sr, sr);
    translate([t + (cw - cs) / 2, t + cw / 2 + cs / 2, -1]) cylinder(2 * t + 2, sr, sr);
}

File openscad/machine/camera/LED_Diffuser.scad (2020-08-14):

$fn = 100;

w = 59;
r = 30 / 2;
l = 10;

t = 2;

r1 = 38 / 2;
r2 = 48 / 2;

difference()
{
    union()
    {
        intersection()
        {
            translate([0, 0, -1]) cube([w, w, t + 1], false);
            translate([w/2, w/2, -1]) cylinder(t + 2, w/2 + 2, w/2 + 2);
        }
        hull()
        {
            translate([0, w/2 - l/2, t]) cube([t, l, 0.1], false);
            translate([1, w/2 - l/2, t + 3]) cube([t, l, 0.1], false);
        }
        rotate([0, 0, 90])
        translate([0, -w, 0])
        hull()
        {
            translate([0, w/2 - l/2, t]) cube([t, l, 0.1], false);
            translate([1, w/2 - l/2, t + 3]) cube([t, l, 0.1], false);
        }
        rotate([0, 0, 180])
        translate([-w, -w, 0])
        hull()
        {
            translate([0, w/2 - l/2, t]) cube([t, l, 0.1], false);
            translate([1, w/2 - l/2, t + 3]) cube([t, l, 0.1], false);
        }
        rotate([0, 0, 270])
        translate([-w, 0, 0])
        hull()
        {
            translate([0, w/2 - l/2, t]) cube([t, l, 0.1], false);
            translate([1, w/2 - l/2, t + 3]) cube([t, l, 0.1], false);
        }
    }
    translate([w/2, w/2, -2]) cylinder(r + 3, r, r);
    difference()
    {
        translate([w/2, w/2, 1]) cylinder(t, r2, r2);
        translate([w/2, w/2, 1]) cylinder(t, r1, r1);
    }
}

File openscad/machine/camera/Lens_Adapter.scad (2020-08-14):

$fn = 100;

r1 = 14.3 / 2;
r2 = 12 / 2;

t = 1.6;
h = 6;

difference()
{
    union()
    {
        hull()
        {
            cylinder(4, r1 + t, r1 + t);
            translate([0, 0, 4]) cylinder(2, r2 + t, r2 + t);
        }
        translate([0, 0, 6]) cylinder(h, r2 + t, r2 + t);
    }
    hull()
    {
        cylinder(4, r1, r1);
        translate([0, 0, 4]) cylinder(2, r2, r2);
    }
    translate([0, 0, 6]) cylinder(h, r2, r2);
}

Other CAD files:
openscad/machine/electronics/stl/LCD_Mount.stl
openscad/toolchanger/stl/Tool_Changer_Bottom.stl
openscad/machine/electronics/stl/PCB_Mount.stl
openscad/machine/y/stl/Y_Tensioner_Mount_Right.stl
openscad/machine/camera/Camera_Top_Mount.scad
openscad/machine/electronics/LCD_Mount.scad
openscad/machine/electronics/PCB_Mount.scad
openscad/machine/electronics/Power_Supply_Case.scad
openscad/machine/electronics/Power_Supply_Cover.scad
openscad/machine/electronics/Vacuum_Pump_Holder.scad
openscad/machine/x/X_Belt_Tensioner_Screw.scad
openscad/machine/x/X_Tensioner_Mount.scad
openscad/machine/x/stl/X_Belt_Tensioner_Screw.stl
openscad/machine/y/Motor_Holder_Y_Left.scad
openscad/machine/y/Tensioner_Nut.scad
openscad/machine/y/X_Rail_Mount.scad
openscad/machine/y/Y_Belt_Tensioner_Screw.scad
openscad/machine/y/Y_GT2_Clamp.scad
openscad/machine/y/Y_Tensioner_Mount_Right.scad
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

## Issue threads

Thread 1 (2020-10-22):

Help me, please! About the marlin.

tshiao4695, 2020-10-22:
Hello! Sir. Can you share me your marlin programing? i making the machine, but I don't had find your programing in your project. can you help me? Thank you! Sir.

mariusmotea, 2021-05-11:
Same issue for me. I made the PNP machine "to print", now i need convert the software to a real PNP one, but the info on google don't help me so much

jamser, 2021-07-19:
Dear Richard Klingler:
     https://github.com/richardklingler/esphome,The link you sent is invalid， that's great jobs for it ,could you send me the eshome.zip or rar ,myemal is:szzs80@163.com,i want to test the WT32-SC01 uses the ST7796S..thank you very much

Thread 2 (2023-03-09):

nozzle holder

ben500, 2023-03-09:
Hello Richard, I like your project, looks good. could you please add a file for the nozzles holder you have in the machine picture?

Hardstyles, 2024-02-24:
Hey Benn, you can find it at https://github.com/richardklingler/openpnp/tree/master/openscad/toolchanger

You can convert the SCAD documents to STL with the online converter.
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

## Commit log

2020-08-14 Added CP40 nozzle holder
    [Tool_Changer.scad, Tool_Changer_Bottom.scad, Tool_Changer_Bottom.stl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]
2020-08-14 Added nozzle holder description
2020-08-14 Moved stl files into own folder
    [Tool_Changer_Bottom.stl, Tool_Changer_Middle.stl, Tool_Changer_Mount.stl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]
2020-08-14 Added picture of mounted tool changer
2020-08-14 Added camera mounts and LED diffuser
    [Camera_Bottom_Mount.scad, Camera_Bottom_Mount.stl, Camera_Top_Mount.scad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]
2020-08-14 Added marlin folder
2020-08-14 Description of Marlin changes
2020-08-15 Added M3 holes for mounting the 3 top layers onto the mount
    [Tool_Changer_Bottom.scad, Tool_Changer_Bottom.stl, Tool_Changer_Middle.scad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]
2020-08-17 Added BOM
2020-08-17 Changed BOM
2020-08-23 Added Y motor mount and tensioner
    [Tensioner_Nut.scad, Tensioner_Nut.stl, Y_Belt_Tensioner_Screw.scad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]
2020-08-23 Added y-axis README
2020-08-23 Added motor mount designs
    [Motor_Holder_Y_Left.scad, Motor_Holder_Y_Left.stl]
2020-08-23 Added x-axis files
2020-08-23 Added y belt clamp
    [Y_GT2_Clamp.scad, Y_GT2_Clamp.stl]
2020-08-23 Moved x-rail mounts into y
    [X_Rail_Mount.scad, X_Rail_Mount.stl]
2020-08-23 Added OpenSCAD electronics
    [LCD_Mount.scad, LCD_Mount.stl, PCB_Mount.scad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]
2020-08-23 Added PSU files
    [Power_Supply_Case.scad, Power_Supply_Case.stl, Power_Supply_Cover.scad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]
2020-08-24 Added vacuum pump holder
    [Vacuum_Pump_Holder.scad, Vacuum_Pump_Holder.stl]
2020-09-12 Added X belt tensioner mount
    [X_Tensioner_Mount.scad, X_Tensioner_Mount.stl]
2020-09-12 Updated X belt tensioner and longer tensioner screw
    [X_Belt_Tensioner_Screw.scad, X_Belt_Tensioner_Screw.stl, X_Tensioner_Mount.scad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]
